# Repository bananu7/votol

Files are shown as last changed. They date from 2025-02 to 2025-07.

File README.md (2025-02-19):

# bananu7/Votol
Hello. This is my repository for all things related to the Votol controllers I was able to gather and put together.

## My use case and context

I'm converting a CRF250 MX motorcycle to electric power, using the Votol EM260SGTP controller. I want to have a bit more control over it that usual, so I decided to learn more about it.
Unless otherwise noted, all descriptions, labels etc. apply to _my specific controller_. Different models of the controller can differ; make sure you understand the cable functions
and model of yours.

## Project structure

* `desktop/` - early beginnings of a desktop app that were meant to replace the original desktop programmer
* `embassy/` - firmware of the display controller that goes on the bike and communicates with Votol EM
* `reference/` - technical details and descriptions of the controller protocol

## Log

### 2025-02-18

I did some more work on the miscellaneous features for the display. Got better frame decoding working, modularized things and importantly created a simulation mode that allows development without a controller connected (still on real hardware, though). I'm still not sure how I want to present all the available data or what peripherals to connect. Ideas list includes:

* all main controller parameters (works for now: battery voltage, temperatures)
* ride mode
* all controller errors in readable format
* temperature alerts
* speed based on the RPM counter
* trip computer: speed * time (distance traveled), current * time (amp-hours used), max/avg speed, max/avg current, moving time

Additional features based on peripheral hw:
* RTC - clock :), configuration (maybe I could use internal RTC)
* SD or flash - datalogger (trip computer but as series)
* IMU, magnetometer - compass, lean-aware TC
* front wheel speed sensor - TC, more accurate speed
* GPS - time, datalogging position
* BT - phone app, remote config and data reading

This is just a mental note to myself; it's unlikely I'll get to doing all of the above. Once I get the basic features working, I'll also upload the CAD files for the enclosure and print a prototype.

### 2025-02-13

I should've started this log immediately, but better late than never. I have already done quite a lot of work, but a lot still remains to be done.
Dealing with the controller can roughly be grouped into two categories:

1) Programming - setting up current and voltage limits, throttle rampup, engine phase config and hall config, as well as pin functions
2) Using - happens in the vehicle

#### Programming

Programming by itself is reasonably straighforward. I need to write more about the programming setup in the reference section, but in short,
the controller comes with a programming USB dongle. This dongle plugs into a two-pin port on the controller colored blue and orange. In my case,
the two-pin interface is a 1M CAN bus, xceived using TJA1050, connecting to an STM microcontroller, then exposed to USB via an USB-to-serial converter.

The controller also comes with a desktop app that looks like it was written with MFC. The app seems to have been made for older, smaller controllers,
and in fact doesn't even show the 260 on the list. To communicate, it opens a serial port at either 9600 or 115200 baud. There's also the CAN
switch that in my case needed to be... disabled. I believe that it's mostly a consequence of historical debt and reuse. The app originally
talked to the controller via serial; once they switched to CAN they were limited to 8-byte data frames, so they added the intermediate translator
chip to the dongle, so that the old app can still talk to the new controller. Incidentally I've noticed that the serial data going back to the app
is 24 bytes long, while the controller only responds with two can frames - so the translator chip must be doing some shuffling and filling in the 
blanks.

I have recorded some of the programming transactions, but haven't saved them. In order to properly reverse engineer the protocol, a whole
communication scheme needs to be observed and the parameters isolated. That being said, as the app seems to work fine for now, this is of low
priority. Perhaps one exciting possibility here would be to replace it with a web-based version talking serial over WebUSB. That would be a massive
usability boost, but getting all controllers working correctly could be a challenge.

#### Using the controller

Much more interesting is what happens during use. I don't want to use the dongle, and CAN is actually a great interface for the vehicle use.
The displays normally utilized with this controller use the separate LIN output, but I see zero reason to do that. CAN is more robust and offers
much more functionality.

The controller exposes a lot of frames on the bus, none of which I've decoded yet. There's been some mentions from SIA that they're their internal
protocol, but nothing concrete about it. I wouldd assume the usual parameters would be broadcasted continously, which would be great for display
purposes.

At the same time, when the desktop app wants live data from the controller, it sends a special query packet. The controller "responds" by sending
two frames containing the vitals; they are described in the reference folder. I was able to successfully read and decode those frames, and
that's the current state in the `embassy` folder; operating on an STM32F103C8 microcontroller, using its onboard CAN controller and TJA1050 
transceiver. On the other end, I plugged in a simple 8x8x4 LED matrix controlled by four MAX7219 chips in series, over SPI. Works great and 
the display of basic parameters has already been achieved.

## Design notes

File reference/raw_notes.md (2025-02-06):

# Reference for communicating with the controller

## Live data read

The cliend sends a 24-byte packet:

```
c9 14 02 53 48 4f 57 00 00 00 00 00 aa 00 00 00 18 aa 00 00 00 00 c4 0d
```

(some other user reported trying to send `c9 14 02 53 48 4f 57 00 00 00 00 00 aa 00 00 00 1e aa 04 67 00 f3 52 0d`).

This is likely something in Chinese, but it also has "SHOW" inside:
```
É..SHOW.....ª....ª....Ä.
```

The controller responds with such a frame; this was gathered while powered at 30V and no motor - that produces
a Hall Fault as well as Undervoltage fault. The fault code is `00000084`. The controller temp is shown as 24C, while
external temp is 190.

```
c0 14 0d 59 42 00 00 00
00 00 00 00 00 84 00 00
4b f0 00 00 01 07 fb 0d
```

### Field reference

```
 0. [ C0 
 1.   14 ]  - controller header

 2. ?
 3. ?
 4. ?

 5. [ xx
 6.   xx ] - 2-byte fixed point battery voltage

 7. [ xx
 8.   xx ] - 2 byte fixed point battery current

 9. ?

10. [ xx
11.   xx
12.   xx
13.   xx ] - 4-byte fault code

14. [ xx
15.   xx ] - 2-byte RPM

16. [ ] - controller temp
17. external temp

20. "gear, antitheft, regen"
21. controller status
22. XOR of first 22 bytes

```

Copied from [Endless Sphere](https://endless-sphere.com/sphere/threads/votol-serial-communication-protocol.112970/).
```
byte B20:{
bit0~1= 0:L, 1:M, 2:H, 3:S
bit2=R
bit3=P
bit4=brake
bit5=antitheft
bit6=side stand
bit7=regen
}

also the detail for status in B21:
0=IDLE
1=INIT
2=START
3=RUN
4=STOP
5=BRAKE
6=WAIT
7=FAULT
```

### Known fault codes:

bits for 4 and 8: hall failure and undervoltage

### CAN field reference - two byte offset

Example dumped frames:
0x3fe = 1022

```
Standard Frame id=3fe [09, 55, aa, aa, 00, 00, 00, 01]
Standard Frame id=3fe [27, 00, 01, 00, 00, 00, 00, 84]
Standard Frame id=3fe [00, 00, 4a, f0, 00, 00, 01, 07]

xx xx xx xx xx xx xx [b
v] [ bc] 00 [ error cd]
[rpm] ct ot xx xx sa sb

```

```
B7~B8:02 14 converts into fixed-point Dec is the battery voltage, for my case it is 53.2V
B9~B10: 00 0f converts into fixed-point Dec is the battery current, for my case is 1.5A
B16~B17: 02 b8 converts into integer is the rpm, for my case is 696
B18: 5d converts into Dec - 50 is the Controller temp, for my case is 43C
B19: 4b converts into Dec - 50 is the External temp, for my case is 25C
B18~B19: 22 d6 converts into integer is the temperature coefficient, for my case is 8918
B22:{
bit0~1= 0:L, 1:M, 2:H, 3:S
bit2=R
bit3=P
bit4=brake
bit5=antitheft
bit6=side stand
bit7=regen
}
```

## Bat voltage/current fixed point

02 14 == 532 -> 53.2V
01 27 == 295 -> ~30V
00 0f == 15 -> 1.5A

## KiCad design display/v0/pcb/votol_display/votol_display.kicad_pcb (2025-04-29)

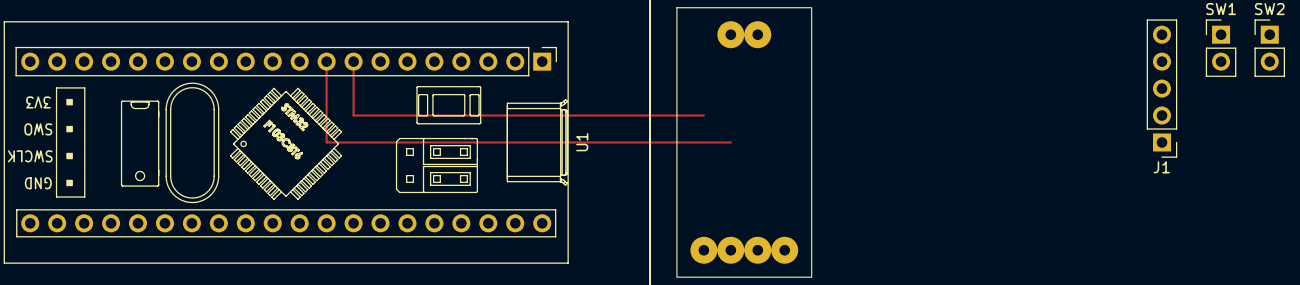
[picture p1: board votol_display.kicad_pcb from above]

Board: 2 copper layers, 5 parts (0 on the bottom side), 6 nets, no tracks yet.

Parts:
J1: Conn_01x05_Pin; PinHeader_1x05_P2.54mm_Vertical
SW1, SW2: SW_Push; PinHeader_1x02_P2.54mm_Vertical
U1: YAAJ_BluePill; YAAJ_BluePill_1
U2: TJA_1050

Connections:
+5V: J1.1, U1.18 (5V), U2.3 (VCC)
CAN_PIN_RX: U1.8 (PA11), U2.5 (TX)
CAN_PIN_TX: U1.9 (PA12), U2.4 (RX)
GND: J1.5, SW1.2, SW2.2, U1.19 (GND), U1.39 (GND), U1.40 (GND), U2.6 (GND)
PIN_BUTTON_1: SW1.1, U1.35 (PB10)
PIN_BUTTON_2: SW2.1, U1.36 (PB11)

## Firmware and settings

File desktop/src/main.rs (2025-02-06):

use std::io::{self, Write};
use std::time::Duration;
use std::{num::ParseIntError};

use clap::{Arg, Command};

pub mod votol;

pub fn decode_hex(s: &str) -> Result<Vec<u8>, ParseIntError> {
    (0..s.len())
        .step_by(2)
        .map(|i| u8::from_str_radix(&s[i..i + 2], 16))
        .collect()
}

fn main() {
    let matches = Command::new("Serialport Example - Receive Data")
        .about("Reads data from a serial port and echoes it to stdout")
        .disable_version_flag(true)
        .arg(
            Arg::new("port")
                .help("The device path to a serial port")
                .use_value_delimiter(false)
                .required(true),
        )
        .arg(
            Arg::new("baud")
                .help("The baud rate to connect at")
                .use_value_delimiter(false)
                .required(true)
                .validator(valid_baud),
        )
        .get_matches();

    let port_name = matches.value_of("port").unwrap();
    let baud_rate = matches.value_of("baud").unwrap().parse::<u32>().unwrap();

    let port = serialport::new(port_name, baud_rate)
        .timeout(Duration::from_millis(10))
        .open();

    // prepare votol mesage
    let votol_str = "c9140253484f570000000000aa00000018aa00000000c40d";
    let votol_question = decode_hex(votol_str).unwrap();

    match port {
        Ok(mut port) => {
            loop {
                match port.write(&votol_question) {
                    Ok(_) => {
                        std::io::stdout().flush().unwrap();
                    }
                    Err(ref e) if e.kind() == io::ErrorKind::TimedOut => (),
                    Err(e) => eprintln!("{:?}", e),
                }

                let mut serial_buf: Vec<u8> = vec![0; 1000];
                println!("Receiving data on {} at {} baud:", &port_name, &baud_rate);

                match port.read(serial_buf.as_mut_slice()) {
                    Ok(t) => {
                        //io::stdout().write_all(&serial_buf[..t]).unwrap();
                        println!("{:#04X?}", &serial_buf[..t]);

                        io::stdout().flush().unwrap();
                    }
                    Err(ref e) if e.kind() == io::ErrorKind::TimedOut => (),
                    Err(e) => eprintln!("{:?}", e),
                }

                std::thread::sleep(Duration::from_secs(1));
            }
        }
        Err(e) => {
            eprintln!("Failed to open \"{}\". Error: {}", port_name, e);
            ::std::process::exit(1);
        }
    }
}

fn valid_baud(val: &str) -> Result<(), String> {
    val.parse::<u32>()
        .map(|_| ())
        .map_err(|_| format!("Invalid baud rate '{}' specified", val))
}

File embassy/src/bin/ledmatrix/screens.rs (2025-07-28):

use crate::ledmatrix::api::{write_battery_bar, write_char, write_fullscreen_float, write_num, write_num_4_digits, write_signed_num_3_digits, write_signed_num_decimal_1k, write_string};
use crate::ledmatrix::compositor::Compositor;
use crate::can::can_frame::{clamp_temp_to_0, get_battery_current, get_battery_voltage, get_controller_temp, get_controller_error, get_external_temp, get_rpm, ThreeVotolFrames, ControllerError};

#[derive(Copy, Clone)]
pub enum DisplayValue {
     Rpm,
     Speed,
     ControllerMotorTemp,
     Voltage,
     Current,
     Power
}

pub fn next(v: DisplayValue) -> DisplayValue {
    match v {
        DisplayValue::Rpm => DisplayValue::Speed,
        DisplayValue::Speed => DisplayValue::ControllerMotorTemp,
        DisplayValue::ControllerMotorTemp => DisplayValue::Voltage,
        DisplayValue::Voltage => DisplayValue::Current,
        DisplayValue::Current => DisplayValue::Power,
        DisplayValue::Power => DisplayValue::Rpm,
    }
}

pub fn ride_screen(frames: &ThreeVotolFrames, value_to_show: DisplayValue, compositor: &mut Compositor, _time_ms: u32) {
    let battery_voltage = get_battery_voltage(&frames);

    let controller_temp = clamp_temp_to_0(get_controller_temp(&frames));
    let external_temp = clamp_temp_to_0(get_external_temp(&frames));
    let rpm = get_rpm(&frames);
    let current = get_battery_current(frames);

    // todo: state or prop?
    match value_to_show {
        DisplayValue::Rpm => {
            let rpm = get_rpm(&frames);
            if rpm < -999 || rpm > 9999 {
                write_signed_num_decimal_1k(rpm, 0, 0, compositor);
            } else if rpm < 0 {
                write_signed_num_3_digits(rpm as i16, 0, 0, compositor);
            } else {
                write_num_4_digits(rpm as i16, 0, 0, compositor);
            }
            write_char(b'%', 19, 0, compositor);
        }
        DisplayValue::Speed => {
            let mut speed = rpm_to_speed(rpm);
            // TODO speeds over 100
            if speed > 99 {
                speed = 99;
            }

            write_num(speed, 12, 0, compositor);
        }
        DisplayValue::Current => {
            write_signed_num_3_digits(current as i16, 0, 0, compositor);
            write_char(b'A', 18, 0, compositor);
        }
        DisplayValue::ControllerMotorTemp => {
            write_num(controller_temp, 0, 0, compositor);
            write_char(b'*', 8, 0, compositor);
            write_num(external_temp, 14, 0, compositor);
            write_char(b'*', 22, 0, compositor);
        }
        DisplayValue::Voltage => {
            write_fullscreen_float(battery_voltage, compositor);
        }
        DisplayValue::Power => {
            write_signed_num_decimal_1k(current * (battery_voltage/10), 0, 0, compositor);
            write_char(b'<', 19, 0, compositor);
            write_char(b'W', 22, 0, compositor);
        }
    }

    write_battery_bar(battery_voltage, compositor);

    let mode_char = get_mode_char(frames);
    write_char(mode_char, 28, 0, compositor);
}

fn rpm_to_speed(rpm: i16) -> u8 {
    // todo: runtime config
    let front_sprocket = 14;
    let rear_sprocket = 60;
    let motor_reduction_a = 20;
    let motor_reduction_b = 47;
    let wheel_circumference = 2138; // mm
    let minutes_in_hour = 60;

    // try to get the number large first
    let speed =
        rpm as i64 // use i64 for more precise math
        * front_sprocket
        * motor_reduction_a
        * wheel_circumference
        / 1000
        * minutes_in_hour
        / (
            rear_sprocket
            * motor_reduction_b
            * 1000
        );

    return speed.abs() as u8;
}

fn get_mode_char(frames: &ThreeVotolFrames) -> u8 {
    let status_byte = frames[2][6];

    // todo bits 5,6,7 - antitheft, sidestand, regen
    return if status_byte & 0b10000 != 0 { // brake
        b'b'
    } else if status_byte & 0b1000 != 0 {
        b'p'
    } else if status_byte & 0b100 != 0 {
        b'r'
    } else if status_byte & 0b010 != 0 {
        if status_byte & 0b1 != 0 {
            b's'
        } else {
            b'3'
        }
    } else {
        if status_byte & 0b1 != 0 {
            b'2'
        } else {
            b'1'
        }
    };
}

/// Converts a ControllerError to a descriptive string
pub fn error_to_string(error: &ControllerError) -> &'static str {
    match error {
        ControllerError::EBrakeOn => "Emergency Brake On",
        ControllerError::OverCurrent => "Hardware Overcurrent",
        ControllerError::UnderVoltage => "Low Battery Voltage",
        ControllerError::ThrottleHallError => "Throttle Hall Error",
        ControllerError::OverVoltage => "High Battery Voltage",
        ControllerError::McuError => "Mcu Error",
        ControllerError::MotorBlock => "Motor Blocked",
        ControllerError::FootplateErr => "Throttle Error",
        ControllerError::SpeedControl => "Runaway Error",
        ControllerError::WritingEeprom => "Program Upload Error",
        ControllerError::StartUpFailure => "Startup Failure",
        ControllerError::Overheat => "Controller Overheat",
        ControllerError::OverCurrent1 => "Software Overcurrent",
        ControllerError::AcceleratePadalErr => "Throttle Failure",
        ControllerError::Ics1Err => "Current Sensor 1 Error",
        ControllerError::Ics2Err => "Current Sensor 2 Error",
        ControllerError::BreakErr => "Brake Failure",
        ControllerError::HallSelError => "Hall Sensor Error",
        ControllerError::MosfetDriverFault => "Driver Failure",
        ControllerError::MosfetHighShort => "Mosfet High Short",
        ControllerError::PhaseOpen => "Phase Wire Open",
        ControllerError::PhaseShort => "Phase Wire Short",
        ControllerError::McuChipError => "Controller Failure",
        ControllerError::PreChargeError => "Pre-charge Failure",
        ControllerError::MotorOverheat => "Motor Overheat",
        ControllerError::SocZeroError => "SOC Zero Error",
    }
}
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

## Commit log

2025-02-06 Switched over to proper remote packages
2025-02-06 Added working SPI (bitbang for now) with max7219
2025-02-07 further librarized ledmatrix
2025-02-07 Working voltmeter
2025-02-07 Added voltage bar display at the botom
2025-02-07 Cleaned up a couple warnings
2025-02-07 Add ledmatrix compositor
2025-02-07 Compositor works, shows both bar and voltage digits
2025-02-18 Add mocked frame
2025-02-18 Moved frame decoding to a separate module
2025-02-18 Add ARM target to rustup
2025-02-18 More frame decoding functions
2025-02-18 Added buttons and showing external temp
2025-02-18 Removed test x3 voltage multiplier
2025-03-16 Added separate error screens
    [can_frame.rs, screens.rs]
2025-03-20 Print current controller status on the right
2025-03-20 Allow negative values for current and voltage
2025-03-20 Actually use motor temperature
2025-03-20 Display temperature grade sign
2025-03-21 Fixed write past bounds
    [screens.rs]
2025-03-21 Better example frame
2025-03-22 Simple mode switch on button press - todo not all modes yet
2025-04-29 Add the screen electricals
    [votol_display.kicad_pcb, votol_display.kicad_sch]
2025-05-28 Add writing controller error to screen
    [screens.rs]
2025-05-28 Pass timer value to screens
2025-05-28 Fix the error bytes location and add to test msg
    [can_frame.rs]
2025-05-28 Scroll error text left
    [screens.rs]
2025-05-28 Fixed error state messages and bytes
    [can_frame.rs, screens.rs]
2025-05-28 Much nicer error state parsing and serialization
    [can_frame.rs, screens.rs]
2025-07-26 very quick screen flip
    [setup.rs]
2025-07-28 Fix fake current, dont crash on negative nums
    [screens.rs]
2025-07-28 Display power in kW
2025-07-28 Various fixes to number and voltage display
    [screens.rs]
